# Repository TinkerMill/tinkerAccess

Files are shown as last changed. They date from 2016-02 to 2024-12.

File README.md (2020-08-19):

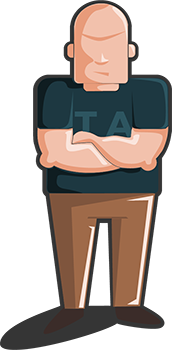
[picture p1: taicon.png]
taicon


# tinkerAccess
The tinkerAccess system is a Raspberry Pi based access control system that can be used to prevent unauthorized users from using devices that require special training. It could also conceivably be used to control electronic lock boxes or doors.

The system was originally designed and created by Matt Stallard, Ron Thomas, and Matt Peopping for TinkerMill a makerspace in Longmont, CO. It is continually being maintained and enhanced by other contributors in the community.

### Install the tinkerAccess system

There are two main components to the system. If you intend to use the client and server software on separate physical devices, then you will want to review the individual documents regarding the installation, configuration, and operation of each respective piece.

- [tinker-access-server](/tinker_access_server/README.md) 
- [tinker-access-client](/tinker_access_client/README.md)

If however, you intend to use both the server and client on the same physical device, then you can follow these simple instructions. You will need to complete these client [prerequisites](/tinker_access_client/docs/prerequisites.md) before running the install script. 

From the Pi terminal:

```
git clone https://github.com/TinkerMill/tinkerAccess.git
cd tinkerAccess
sudo bash install.sh
```

After running the installation script, the configuration files for both the server and client are created, but they need to be modified for a proper setup, before rebooting or restarting the services to take effect.

Edit the server configuration file:

```
sudo nano /opt/tinkeraccess/server.cfg
```

Edit the client configuration file:

```
sudo nano /etc/tinker-access-client.conf
```

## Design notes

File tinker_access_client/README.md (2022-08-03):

# tinker-access-client

The tinker-access-client is the client piece of the tinkerAccess system, a [Raspberry Pi](https://www.raspberrypi.org/products/) based access control system that can be used to prevent unauthorized users from using devices that require special training. It could also conceivably be used to control electronic lock boxes or doors.

The system was originally designed and created by [Matt Stallard](https://github.com/mstallard), [Ron Thomas](https://github.com/RonaldThomas), and [Matt Peopping](https://github.com/analogpixel) for [TinkerMill](http://www.tinkermill.org) a makerspace in [Longmont, CO](https://www.google.com/maps/place/Longmont,+CO/@40.1679379,-105.1678944,12z/data=!3m1!4b1!4m5!3m4!1s0x876bf908d5cc3349:0xc17da1eef3a32735!8m2!3d40.1672068!4d-105.1019275). It is continually being maintained and enhanced by other contributors in the community.

The client software is a [Python 2.7](https://www.python.org/download/releases/2.7/) service designed to run on the [Raspberry Pi OS](https://www.raspberrypi.org/downloads/raspberry-pi-os/). The service is responsible for coordinating activity between the RPi's peripherals (i.e., RFID reader, LCD, etc.) and the GPIO, as well as communicating with the [tinker-access-server](/tinker_access_server/README.md) for activity logging, authentication, and authorization.

Official releases of the client software are packaged and published to [PyPI - the Python Package Index ](https://pypi.python.org/pypi/tinker-access-client/)  

## Prerequisites
You will need to complete these [prerequisites](docs/prerequisites.md) before installing the tinker-access-client.

## Installing the tinker-access-client:

By default, the tinker-access-client is installed as a service that starts immediately, as well as upon reboot of the device.

Use the following command to get the latest version of the client:
```
sudo pip install --upgrade --force-reinstall --ignore-installed --no-cache-dir tinker-access-client --no-binary tinker-access-client
```

Query the client status:
```
sudo tinker-access-client status
```

If the client successfully starts, then the expected status should be *'idle'*. However, the client service will likely not start up at first, and the returned status will be *'terminated'*. The reason for this is that the default client configuration settings will likely not work without some changes. Therefore a client configuration file needs to be added and modified. Get an example client config file directly from the GitHub repo, and then modify it:
```
sudo wget https://raw.githubusercontent.com/TinkerMill/tinkerAccess/master/tinker_access_client/config_file/tinker-access-client.conf -P /etc --backups=1
sudo nano /etc/tinker-access-client.conf
```

The example configuration file has the most commonly used options, many of which are commented out. The *Options* section below lists all of the possible options that can be set in the config file. The command line configuration options all start with --, but the equivalent config file name to be used in the config file is shown in square brackets [ ]. Modify the config file to match your tinker-access-client node wiring and setup, then save the file.

Start the client service again and recheck the status:
```
sudo tinker-access-client start
sudo tinker-access-client status
```

If the client status still does not come back as *'idle'*, then check the log file to get an idea as to why the client service is not starting:
```
less /var/log/tinker-access-client.log
```

See the [development guide](docs/development.md) for special installation instructions, best practices and other helpful information for maintaining and enhancing the code for the future.

## Upgrading the tinker-access-client:

To upgrade to the latest version of the client, here are the commands that have worked for me:
```
sudo tinker-access-client stop
sudo pip install --upgrade --force-reinstall --ignore-installed --no-cache-dir tinker-access-client --no-binary tinker-access-client
sudo tinker-access-client --version
sudo tinker-access-client status
```

## Downgrading the tinker-access-client:

To downgrade to a previous version of the client, here are the commands that have worked for me. Replace the version number in the 'pip install' line with the actual desired version number:
```
sudo tinker-access-client stop
sudo tinker-access-client remove
sudo pip install --upgrade --force-reinstall --ignore-installed --no-cache-dir tinker-access-client==2020.6.28.24 --no-binary tinker-access-client
sudo tinker-access-client --version
sudo tinker-access-client status
```

## Using the tinker-access-client command-line tools:
The remaining information in this guide explains some ways to customize the behavior of the client, control the client, and/or get feedback about the state of the client.

All of the following commands and options are available by using the  --help option on the command line.
```
sudo tinker-access-client --help
```

#### Usage:
```
sudo tinker-access-client <command> [options]
```

#### Commands:
- __start__ : This command will start the tinker-access-client process.

- __stop__ : This command will stop the tinker-access-client process.

- __status__ : This command will return the current state of the tinker-access-client (i.e. initialized, idle, in_use, in_training, terminated).

- __update__ : This command will update the tinker-access-client from the [PyPI - the Python Package Index ](https://pypi.python.org/pypi/tinker-access-client/).  

  By default, the latest published version will be installed. Optionally, a second argument can be provided to specify the specific version desired.
  ```
  sudo tinker-access-client update 2017.2.14.441
  ```

- __remove__ : This command will stop the tinker-access-client process, remove the service and all other artifacts installed via PIP.  

- __restart__ : This command will stop and restart the tinker-access-client process, this can be useful to reload after code changes.

#### Options:

The default value of most of these options can be overridden in a config file. Specifying options via the command line can be useful for debugging purposes.

For example creating this file would enable the auto_update feature, and set the logging level to debug:  

File: `/etc/tinker-access-client.conf`
```
[config]
log_level: 10
auto_update: true
```

- __--version__: Show the current version number and exit

- __-h, --help__: Show the help message and exit

- __--config-file=[config_file]__: The location of the config file to use [default:'/etc/tinker-access-client.conf'] a non-default command-line option value will have precedence over a config-file option value

- __--logging-config-file=[logging_config_file]__: The location of a logging config file to use [default:'/etc/tinker-access-client.logging.conf'] If this file is present, it will override the default logging configuration including the --log-level and --log-file options

- __--debug__: Run in the foreground (a.k.a debug mode) [default:'False']

- __--force-update__: By default, the update command will not do an update if the current version matches the latest version published to [PyPI - the Python Package Index ](https://pypi.python.org/pypi/tinker-access-client/). This option bypasses the version check, and will force a re-install [default:'False']

- __--auto-update=[auto_update]__: If configured, the client will periodically check if a newer version has been published to [PyPI - the Python Package Index ](https://pypi.python.org/pypi/tinker-access-client/). If a new version is found, it will be install it automatically.
[default:'False']

- __--auto-update-interval=[auto_update_interval]__: The period (specified in minutes) that the [PyPI - the Python Package Index ](https://pypi.python.org/pypi/tinker-access-client/) should be checked for a new version of the client. [default:5]

- __--log-file=[log_file]__: The path and name of the log file [default:'/var/log/tinker-access-client.log']

- __--status-file=[status_file]__: The path and name of the status file, the contents of this file will always reflect the current state of the client. (i.e. initialized, idle, in_use, in_training, terminated) A missing file indicates the client is not running [default:'/var/log/tinker-access-client.status']

- __--pid-file=[pid_file]__: The path and name of the client daemon's pid file [default:'/var/run/tinker-access-client.pid']

- __--log-level=[log_level]__: The log level to use [default:40]

- __--server-address=[server_address]__: The [tinker-access-server's](../tinker_access_server/README.md) api address
[default:'http://localhost:5000']

- __--device-id=[device_id]__: The unique identifier for this client, as configured in the [tinker-access-server](../tinker_access_server/README.md) [default:'none']

- __--logout-coast-time=[logout_coast_time]__: A fixed number of seconds to wait for the physical machine to stop before disabling power, after the current sense pin goes low. (i.e., a blade to stop spinning etc...) [default:0]

- __--max-power-down-timeout=[max_power_down_timeout]__: The maximum number of seconds to wait for the current sense pin to go low during logout/shutdown [default:None(infinite)]

- __--reboot-on-error=[reboot_on_error]__: Any unhandled errors will cause the device to reboot after the specified --reboot-delay. [default:'False']

  This behavior is only supported on Raspberry Pi devices.

- __--reboot-delay=[reboot_delay]__: The number of seconds to wait before attempting to reboot the device after an unhandled error. [default:5]

- __--pin-logout=[pin_logout]__: The logout button pin [default:16]

- __--pin-power-relay=[pin_power_relay]__: The power relay pin [default:17]

- __--pin-led-red=[pin_led_red]__: The red led pin [default:21]

- __--pin-led-green=[pin_led_green]__: The green led pin [default:19]

- __--pin-led-blue=[pin_led_blue]__: The blue led pin [default:20]

- __--pin-current-sense=[pin_current_sense]__: The current sense pin [default:12]

- __--pin-current-threshold=[pin_current_threshold]__: The current sense detect threshold PWM pin [default:18]

- __--pin-estop=[pin_estop]__: The E-STOP input pin [default:6]

- __--pin-bypass-detect=[pin_bypass_detect]__: The bypass detect input pin [default:13]

- __--pin-3v3-en=[pin_3v3_en]__: The 3.3V enable pin [default:27]

- __--pin-alarm=[pin_alarm]__: The alarm output pin [default:22]

- __--use-estop=[use_estop]__: The E-STOP input pin will be used to detect E-STOP events and automatically logout the user [default:'False']

- __--estop-active-hi=[estop_active_hi]__: The E-STOP input pin is detected as active high if true, otherwise the input is active low [default:'False']

- __--use-bypass-detect=[use_bypass_detect]__: The bypass detect input pin will be monitored to log a tamper or bypass event [default:'False']

- __--use-3v3-en=[use_3v3_en]__: The PCB has a 3.3V enable output pin and will be cycled during start-up or certain errors. This feature should be set for PCB rev 1.4 or higher [default:'False']

- __--use-alarm=[use_alarm]__: The alarm output pin is enabled and will output high during an alarm condition [default:'False']

- __--use-pgm-current-threshold=[use_pgm_current_threshold]__: The PCB has a programmable current detect threshold PWM output and will be set during init to set the current detect threshold. This feature is available on PCB rev 1.4 or higher. If current detection is desired on rev 1.4 PCBs, this feature must be set True. If it is not desired, it can be left set to False [default:'False']

- __--current-detect-setting=[current_detect_setting]__: The current sense detect threshold setting in RMS milliamps [default:'10000']

- __--ct-burden-resistor=[ct_burden_resistor]__: The current transformer burden resistor value in ohms [default:'1000']

- __--ct-turns-ratio=[ct_turns_ratio]__: The current transformer turns ratio [default:'2000']

- __--is-a-door=[is_a_door]__: The device is a door. If defined, it changes the default behavior of the device and enables the remaining door parameters below [default:'False']

- __--door-unlock-time=[door_unlock_time]__: The amount of time the door unlocks in seconds. Only used if the is-a-door parameter is also enabled [default:'10']

- __--door-continuous-unlock=[door_continuous_unlock]__: The door is defined as being able to be held in a continuously unlocked state. Only used if is-a-door parameter is also enabled. This parameter should only be used on door locks that can be left permanently energized. It should not be enabled on non-continuous duty solenoid style locks. The logout button will be used to toggle between the locked and unlocked state. Therefore, the training mode will be disabled if this parameter is set [default:'False']

- __--door-normal-hr-start=[door_normal_hr_start]__: The start of normal hours, when a door can be held in a continuously unlocked state. Only used if is-a-door and door-continuous-unlock parameters are also enabled. The time is defined in 24hr format. The door cannot be held in an unlocked state before this time [default:'730']

- __--door-normal-hr-end=[door_normal_hr_end]__: The end of normal hours, when a door can be held in a continuously unlocked state. Only used if is-a-door and door-continuous-unlock parameters are also enabled. The time is defined in 24hr format. The door will lock if currently unlocked at this time and cannot be held in an unlocked state after this time [default:'2200']

- __--disable-training-mode=[disable_training_mode]__: Disables entering training mode at the device if the logout button is held down for 3 seconds [default:'False']

- __--serial-port-name=[serial_port_name]__: The serial port attached to the RFID reader [default:'/dev/ttyUSB0']

- __--serial-port-speed=[serial_port_speed]__: The serial port speed to use [default:9600]

- __--display-serlcd=[display_serlcd]__: Send commands for the SparkFun LCD-14072 SerLCD display if true, otherwise send commands for the original backpack style display [default:'False']

- __--allow-user-override=[allow_user_override]__: Allows a new user to login and takeover the current user login session [default:'False']

## Tuning the current detection threshold:

Newer PCBs (rev 1.4) have a programmable current detection threshold. Details on how to tune this can be found [here](tuning/README.md).

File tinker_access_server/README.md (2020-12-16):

# tinker-access-server
All the commands below should be executed from the terminal on the relevant TinkerAccess server.

#### Manage the Services

To start/stop/restart the server:
```
sudo service tinkerserver [start/stop/restart]
```

To stop/start/restart the client:
```
sudo service tinkerclient [start/stop/restart]
```

### Device administration
Incorrectly removing a device can cause big problems and
is rarely needed, so the functionality to modify devices
is located in the cli program devicemanager.py.  This program will allow
you to add, delete, and rename a device.

#### Add a new device 
```
cd /opt/tinkeraccess
sudo ./devicemanager.py -a -n "<new device name>"
```
#### Delete a device
This will delete the device from the database, and it will also delete
all user access records from the database. (not user accounts, but
the fact they have access to the device you just deleted.)
```
cd /opt/tinkeraccess
./devicemanager.py -l
sudo ./devicemanager.py -d -i <device ID to be deleted>
```
#### Rename a device
```
cd /opt/tinkeraccess
sudo ./devicemanager.py -r -i <device ID for name change> -n "<new device name>"
```
#### Grant all users access to a device
This command will grant all users access to the device. Any user in the database will be authenicated to use the device. This command
sets the all users column of the device table
```
cd /opt/tinkeraccess
./devicemanager.py -l
sudo ./devicemanager.py -u -i <device ID to grant all user access>
```
#### Remove all users access to a device
This command sets up the device access level on a per user basis. Users will need to be specifically granted access to be authenicated to use the device. This command
clears the all users column of the device table
```
cd /opt/tinkeraccess
./devicemanager.py -l
sudo ./devicemanager.py -c -i <device ID to remove all user access>
```

### User Administration
#### Adding a new user
To add a new user, scan their badge on the card reader.  Once scanned
if the users badge code is not in the database already, the user
will be added to an Inactive Users table.  On the web gui go to:
http://serverip:5000/admin/interface/newuser  and grant access to
the badge you just swiped.
#### Editing a user
once a user exists in the system, you can use the Users tab to modify
what they have access to.  go to http://serverip:5000/admin/interface/user,
select the pencil next to the user you want to edit, and then from there
you can remove or grant access to all the devices currently registered
in the database

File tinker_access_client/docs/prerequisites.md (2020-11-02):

# Prerequisites:
1. Build the custom tinkerAccess [Raspberry Pi HAT](https://www.raspberrypi.org/blog/introducing-raspberry-pi-hats/) as described [here](/Hardware/PCBs/TinkerAccess/).

2. Create a [Raspberry Pi OS](https://www.raspberrypi.org/downloads/raspberry-pi-os/) boot image as described in detail [here](bootimage.md).

3. Modify the Raspberry Pi Configuration.

   Launch the 'Raspberry Pi Configuration' as shown below:

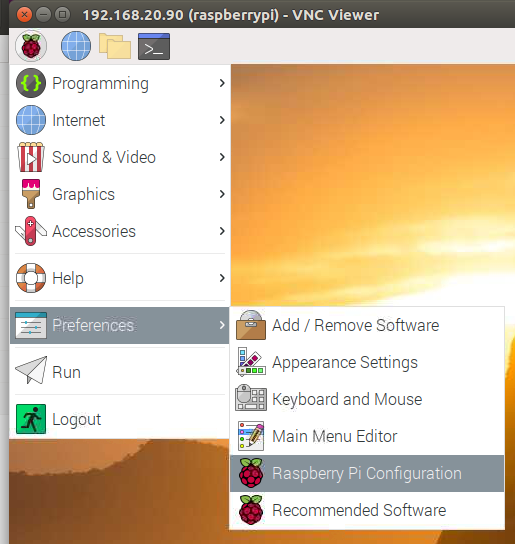
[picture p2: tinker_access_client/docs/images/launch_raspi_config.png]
Raspberry Pi Configuration
   

   Change the Hostname of the client, and change the default password if not completed in an earlier step:

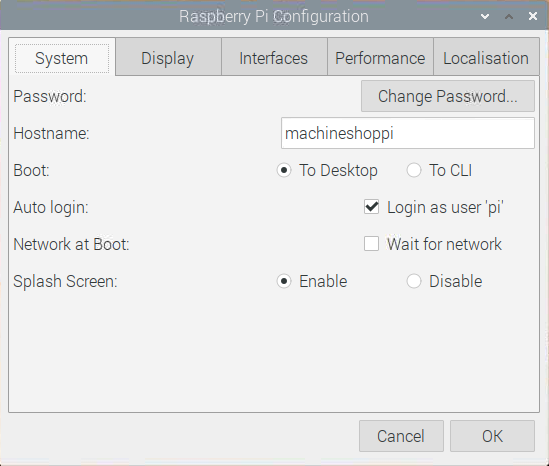
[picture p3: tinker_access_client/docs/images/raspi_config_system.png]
Pi Config System
   

   Setup the Interfaces as shown below:

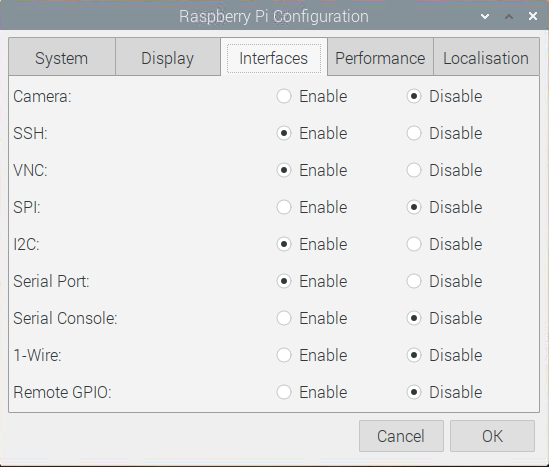
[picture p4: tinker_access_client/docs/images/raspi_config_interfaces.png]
Pi Config Interfaces
   

   SSH and VNC should be enabled for headless remote access to the client. 'I2C' needs to be enabled for the client to communicate to the LCD display. The 'Serial Port' needs to be enabled for the client to communicate to the RFID, but the 'Serial Console' needs to be disabled so that it does not interfere with the RFID communication.

   Reboot the Pi after making changes to the Raspberry Pi Configuration.

4. Reconnect to your Pi via [SSH](https://www.raspberrypi.org/documentation/remote-access/ssh/README.md) or [VNC](https://www.raspberrypi.org/documentation/remote-access/vnc/README.md).

5. Install the python package manager (a.k.a 'pip').

   **IMPORTANT**: If you have just created a new image using the previous mentioned guide, or you are using an existing image...

   Ensure you have the latest version of [pip](https://pip.pypa.io/en/stable) and its related setuptools installed. If you do not complete this step, you will almost certainly __not__ have a good time. Version issues with PIP and its related setuptools can be inconsistent, confusing, and difficult to resolve. It is better to just avoid it now and ensure that they are updated. 

   Many references that you can find, say to upgrade pip with the command 'pip install --upgrade pip setuptools'. However, it is not advisable to upgrade the system version of pip with this method. It can create all sorts of issues if the system maintainer version is upgraded via this method. References to many of these issues are described [here](https://github.com/pypa/pip/issues/5599).

   The recommended upgrade process is shown below:
   ```
   sudo apt update
   sudo apt install python-pip python-setuptools
   ```

6. Install pigpio

   For the PWM current sense level detect output, the Python code uses the PWM features of the pigpio library. Therefore, the pigpio library needs to be installed and the daemon needs to be started at bootup. The following command will ensure the pigpio library is installed and the daemon running at bootup:
   ```
   sudo apt install pigpio
   sudo systemctl enable pigpiod
   sudo reboot
   ```

   After reboot check the status of the pigpiod daemon with the following command:
   ```
   sudo systemctl status pigpiod
   ```
   
7. Continue with [client only install](/tinker_access_client/README.md) or [combined client/server install](/README.md).

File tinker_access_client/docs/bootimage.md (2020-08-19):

## Creating a tinker-access-client boot image:

This document details the steps required to create a [Raspberry Pi OS](https://www.raspberrypi.org/downloads/raspberry-pi-os/) boot image and prepare it for the tinker-access-client.

There are many such guides that you can find, some with much more info, some with much less. I will let you pick your own poison, but it is hard to beat [this guide](https://www.raspberrypi.org/documentation/installation/installing-images/README.md).

The intent of this guide is to document a few additional steps that will facilitate the install in a completely headless mode (i.e., not requiring a monitor and keyboard). In order to do a completely headless setup, there needs to be a method to determine the IP address assigned to the Pi, external to the Pi. Access to the network router/DHCP server would typically be the desired method. If such a method is not available, then the initial stages of setup will need to use a monitor and keyboard, until the IP address can be determined and the SSH and/or VNC services enabled. After that, the setup can continue in a headless mode.

1. Download the [Raspberry Pi OS image](https://www.raspberrypi.org/downloads/raspberry-pi-os/).

   The "Raspberry Pi OS (32-bit) with desktop" is the typical desired image. It is a somewhat light-weight image, in that it does not include all of the recommended software of a full install, but it still includes the desktop.

2. Write the image to an SD card.

   Using your preferred method, write the downloaded image to an SD card. The standard method is the [Raspberry Pi Imager](https://www.raspberrypi.org/documentation/installation/installing-images/README.md). Other methods are described in the link for various OSes.

#### Steps 3-8 are optional. If you do not want to begin the install in a completely headless mode, and are starting with a keyboard and monitor, you can install the imaged SD card in the Pi, power it up, and continue the setup starting at step 9.

3. Mount the *boot* partition of the SD card locally, so that you can add a couple of files to the root directory of the *boot* partition.

4. [Enable SSH for a headless Pi](https://www.raspberrypi.org/documentation/remote-access/ssh/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).

   Create an empty file named *ssh* at the root of the *boot* partition. This will automatically enable the SSH service when the Raspberry Pi boots up, which is normally disabled by default.

   From the root directory of the locally mounted *boot* partition, run the following command:
   ```
   sudo touch ssh
   ```

5. [Setup WiFi for a headless Pi](https://www.raspberrypi.org/documentation/configuration/wireless/headless.md).

   Create a file named *wpa_supplicant.conf* in the root directory of the *boot* partition that contains your WiFi credentials. On the initial boot, the Raspberry Pi will copy this file to the appropriate location and use it to connect to your WiFi network so that you can continue to configure it via SSH.

   From the root directory of the locally mounted *boot* partition, run the following command:
   ```
   sudo nano wpa_supplicant.conf
   ```

   Paste the following contents into the file and save. Modify the SSID and password to match your actual WiFi access point credentials.
   ```
   ctrl_interface=DIR=/var/run/wpa_supplicant GROUP=netdev
   update_config=1
   country=US
   
   network={
    ssid="<Name of your wireless LAN>"
    psk="<Password for your wireless LAN>"
   }
   ```

6. Unmount the *boot* partition, remove the SD card, install it in the Raspberry Pi, and power it up.

7. Enable the VNC server to facilitate completion of the install via the desktop on a VNC client running locally.

   From your local machine, ssh into the Raspberry Pi. Use the actual IP address assigned to the Pi. For the default *pi* username, the default password is *raspberry*:
   ```
   ssh pi@192.168.20.90
   ```

   Enable the VNC server via *raspi-config*:
   ```
   sudo raspi-config
   ```

   Select *Interfacing Options* from the raspi-config menu:

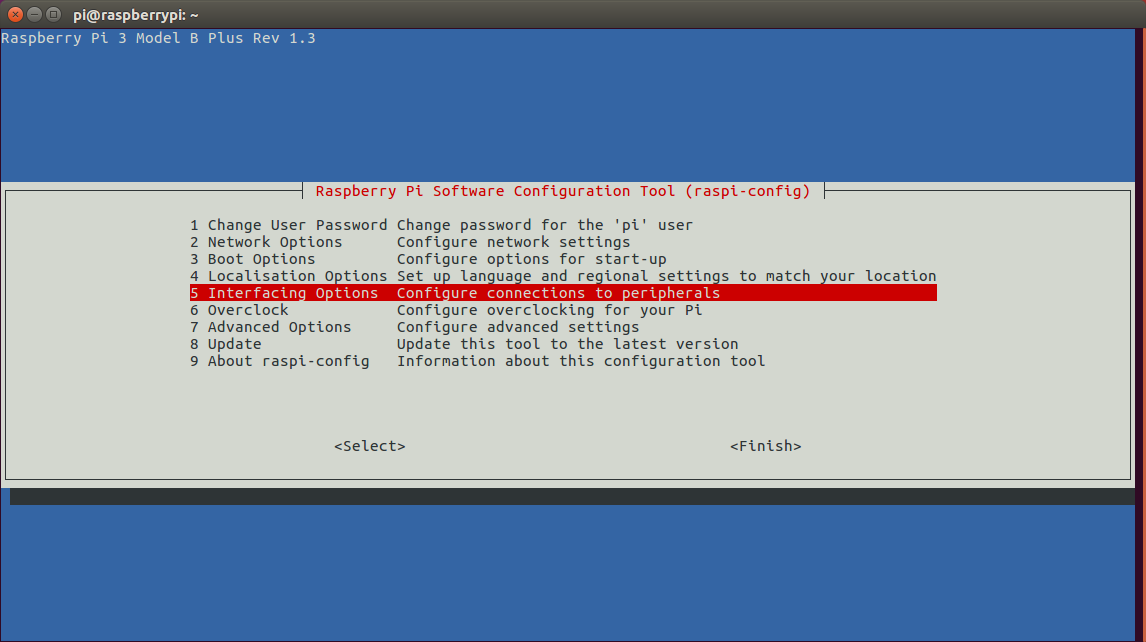
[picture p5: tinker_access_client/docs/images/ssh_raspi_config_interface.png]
raspi-config Interfacing Options
   

   Next, select *VNC* from the raspi-config menu, and then enable the VNC server.

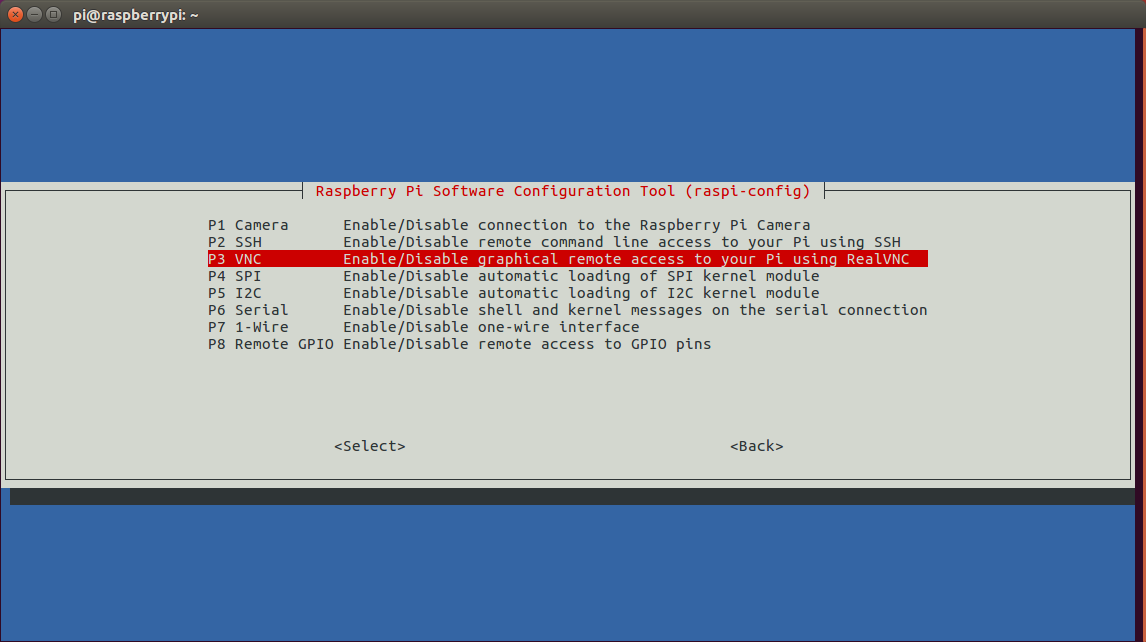
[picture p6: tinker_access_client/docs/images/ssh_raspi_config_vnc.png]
raspi-config VNC
   

   After enabling the VNC server, exit the raspi-config, and exit the SSH session. The VNC server should be started and does not require a reboot of the Pi.

8. Connect to the Raspberry Pi via a RealVNC Viewer client running on your local machine.

   Use the assigned IP address to connect and use the default username *pi* and password *raspberry*. The default password can be changed in the next step.

9. Complete the Raspberry Pi OS installation and update.

   After the initial boot, the following dialog box should be displayed to continue the installation process. Click 'Next' to continue the setup:

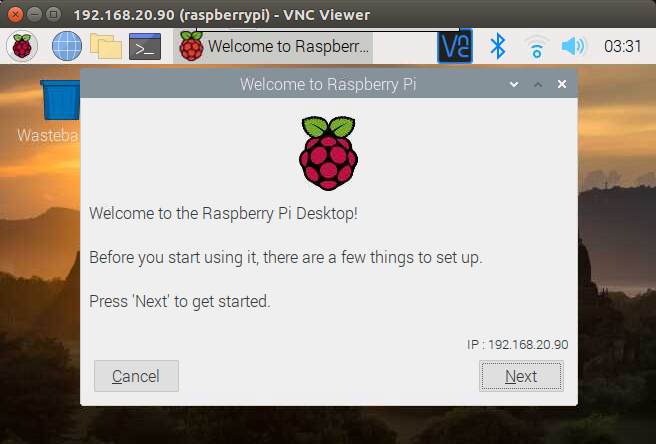
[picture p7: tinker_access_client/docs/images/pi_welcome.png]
Installation Welcome
   

   Set the Country and Timezone:

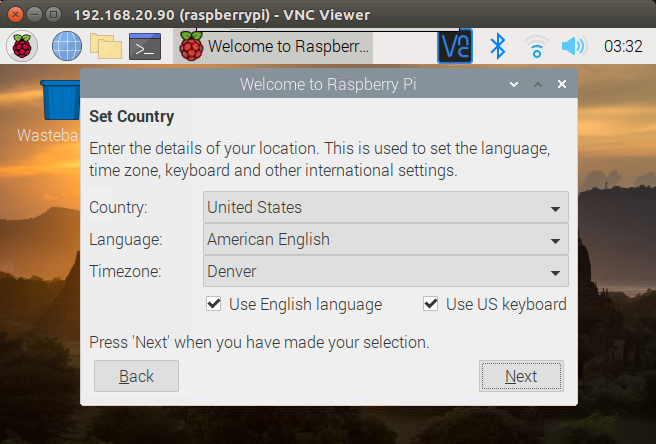
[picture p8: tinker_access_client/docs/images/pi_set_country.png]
Installation Set Country
   

   Change the default *pi* username password in this step:

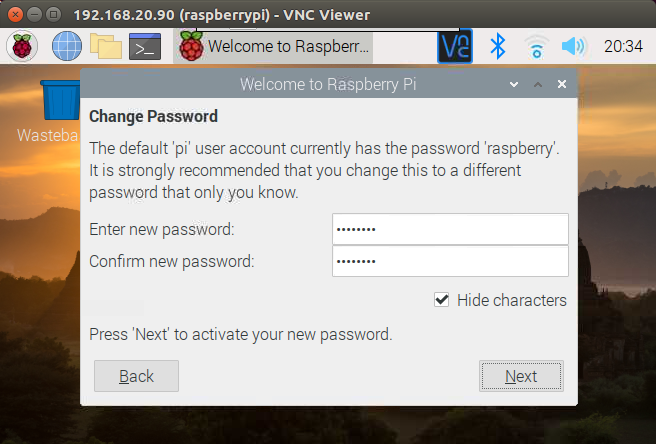
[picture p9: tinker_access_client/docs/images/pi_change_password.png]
Installation Change Password
   

   Leave the 'fill entire screen' checkbox unchecked:

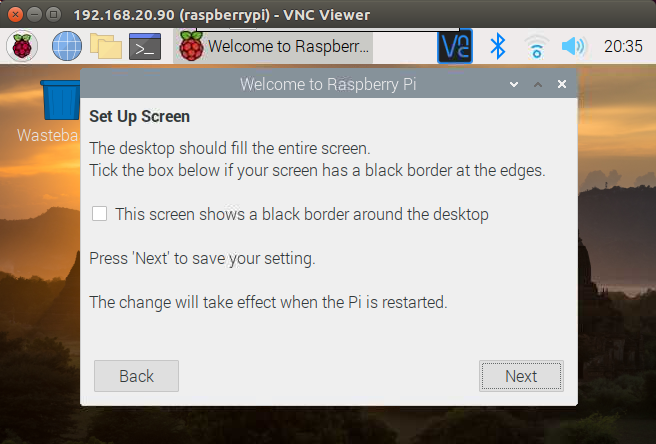
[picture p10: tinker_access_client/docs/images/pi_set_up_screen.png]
Installation Set Up Screen
   

   Click 'Next' to download and install updates to the OS. This will take a while to complete:

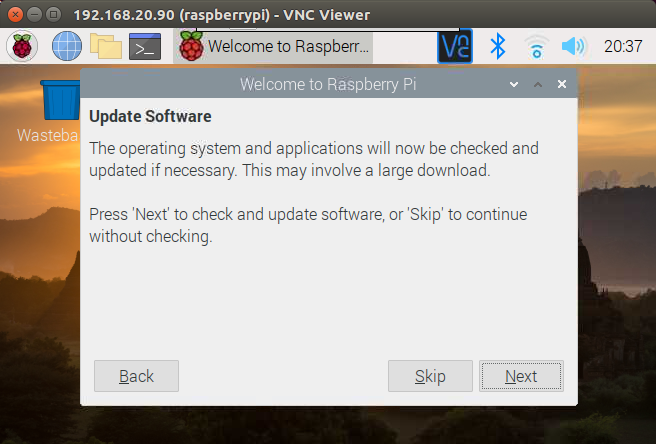
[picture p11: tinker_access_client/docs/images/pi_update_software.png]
Installation Update Software
   

   If the download and update fails for any reason, the update can be completed at the command line with the following commands:
   ```
   sudo apt update
   sudo apt upgrade
   ```

   After the update completes, the following dialog will be displayed. If you want to change the default screen resolution when connected to the Pi via VNC, without a monitor, do not reboot just yet, and click 'Later'. Complete step 10 before rebooting. Otherwise, if you do not want to change the default screen resolution, go ahead and reboot the Pi by clicking 'Restart':

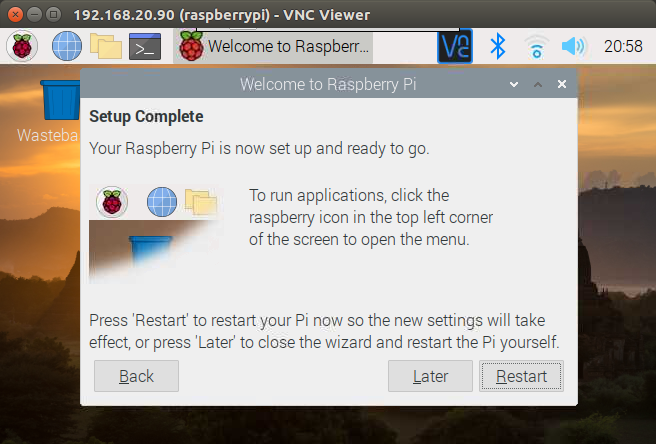
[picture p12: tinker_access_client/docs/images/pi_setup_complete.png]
Installation Setup Complete
   

10. Change the default screen resolution.

    This step is optional, but should be completed if you want the default VNC screen resolution to be something larger, when no monitor is connected. Edit the */boot/config.txt* file to change the default screen resolution. From a terminal window on the Pi, run the following command:
    ```
    sudo nano /boot/config.txt
    ```

    Uncomment and modify the contents of the following lines to look like the following. This will change the screen resolution to CEA mode, 1920x1080, 60Hz, 16:9 aspect ratio:
    ```
    # uncomment if hdmi display is not detected and composite is being output
    hdmi_force_hotplug=1
    
    # uncomment to force a specific HDMI mode (this will force VGA)
    hdmi_group=1
    hdmi_mode=16
    ```

    Reboot the Pi:
    ```
    sudo reboot
    ```
    
#### The setup of the Raspberry Pi OS boot image for the tinker-access-client is complete. You can continue with the rest of the client [prerequisites](prerequisites.md)

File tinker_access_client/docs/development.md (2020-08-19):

### Development:

For development purposes, the client code can be installed from many different types of locations (i.e., the local file system and other [GitHub](https://github.com) branches). You can find additional examples [here](http://www.developerfiles.com/pip-install-from-local-git-repository/).

You can use the [-e, --editable](https://pip.pypa.io/en/latest/reference/pip_install/#cmdoption-e) flag to install the package in editable mode. This will create a symlink from dist-packages to your local development directory so you do not need to re-install each time you change a file.
```
sudo pip install -e <path to your local development directory where setup.py resides>
```

I generally do not do development on the Raspberry Pi. I setup a task to synchronize my files from my development machine and the Pi. PyCharm makes this easy with [deployment configuration](https://www.jetbrains.com/help/phpstorm/2016.3/deployment.html), but there are many other options to synchronize a directory with a remote directory.

Here are examples of my [connection](images/deployment_configuration_connection.png) & [mappings](images/deployment_configuration_mappings.png) configuration.

After changing a local file, ssh into the Raspberry Pi and restart the client software to see your changes take affect.
```
sudo tinker-access-client restart
```

##### Run in stand-alone mode:

When you install the client using [-e, --editable ](https://pip.pypa.io/en/latest/reference/pip_install/#cmdoption-e) option flag, the client will NOT install the service piece. You will get the command line support tools, but you will not automatically get the service piece. This means that any service related commands will not work (i.e., *sudo service tinker-access-client start*) and the client will not automatically start upon boot of the device.

If you really do want the service piece, you can create it with these commands, pointing the symlink to the same location that you installed your package from using the -e flag. Normally this is not required.
```
# create the startup service symlink manually
sudo ln -sf ~/projects/tinkerAccess/tinker_access_client/tinker_access_client/Service.py /etc/init.d/tinker-access-client

# grant execute permission on the Service.py file
sudo chmod 0755 ~/projects/tinkerAccess/tinker_access_client/tinker_access_client/Service.py

#configure the service to start on boot
sudo update-rc.d -f tinker-access-client defaults 91

#start the service
sudo service tinker-access-client start
```

You can run the client as a stand alone script in the foreground if you do not want to install a full blown service. This is helpful for testing and development purposes. You can also control the configuration in debug mode with additional command line switches. However, if you want complete control via the command line, and do not want the config file overriding your command line switches, be sure to rename or delete the */etc/tinker-access-client.conf* file.
```
sudo tinker-access-client start --debug
```

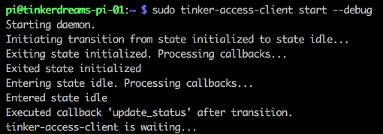
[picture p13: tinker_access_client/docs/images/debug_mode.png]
debug


### Testing/Emulation:

See the [testing](/tinker_access_client/tests/README.md) documentation for more info.

### Logging:

If you are not using debug mode, but want to watch the log messages you can use the following command:
```
sudo tail -f /var/log/tinker-access-client.log
```

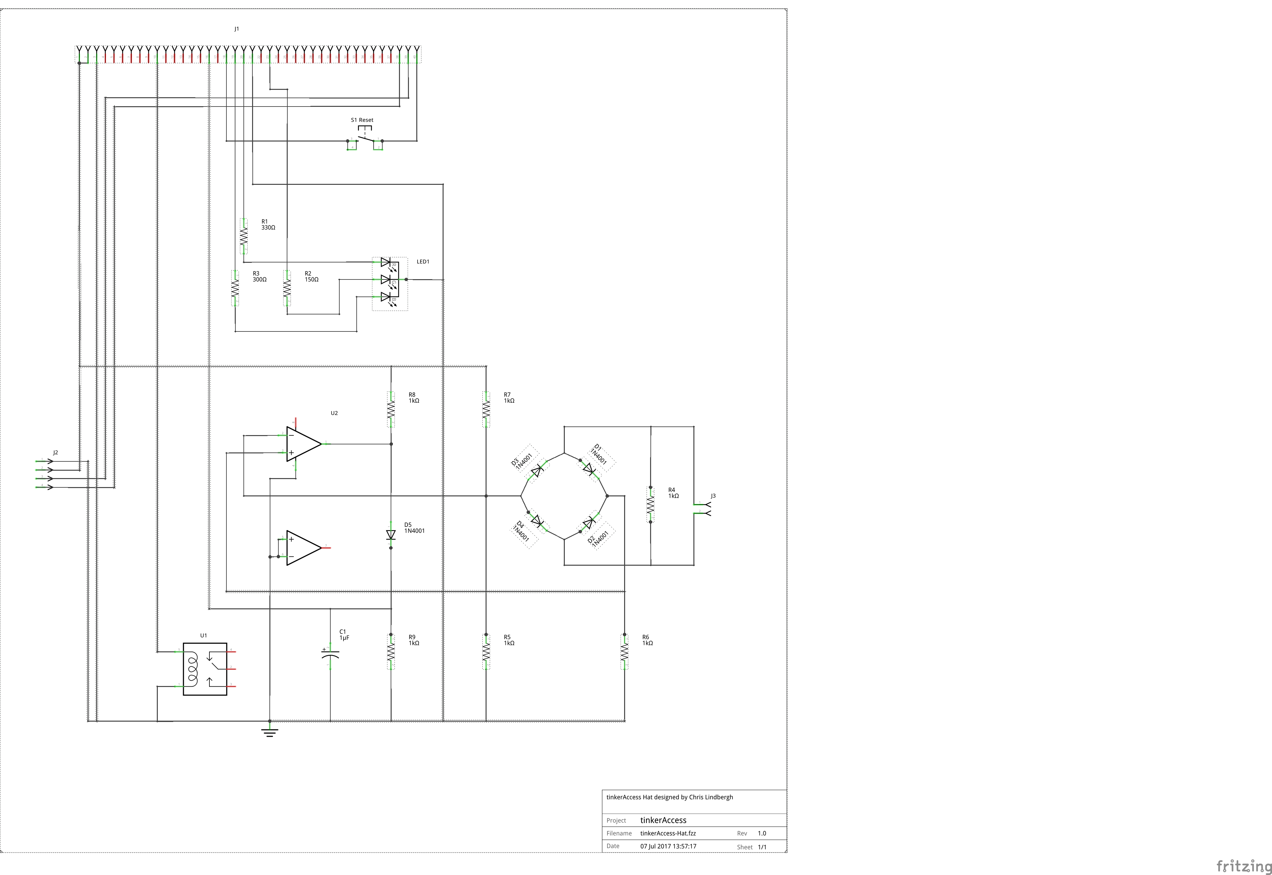
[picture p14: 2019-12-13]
docs/PCBFiles/tinkerAccess-Hat_schem.png

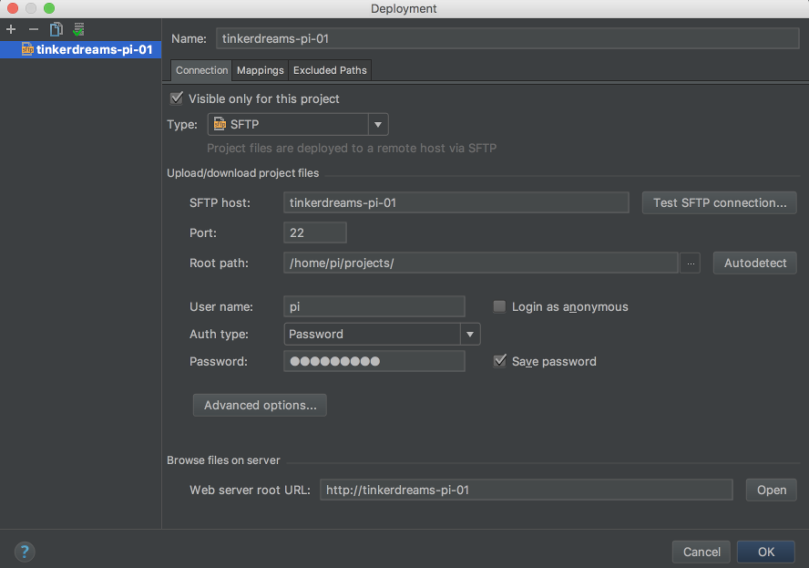
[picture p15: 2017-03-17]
tinker_access_client/docs/images/deployment_configuration_connection.png

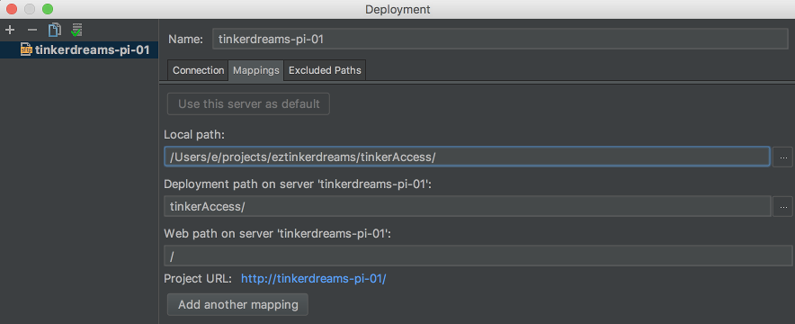
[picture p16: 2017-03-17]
tinker_access_client/docs/images/deployment_configuration_mappings.png

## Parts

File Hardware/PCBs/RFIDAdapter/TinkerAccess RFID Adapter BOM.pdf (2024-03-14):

# TinkerAccess RFID Adapter v1.0 BOM

RefDes | Qty | Description | Package / Footprint | Manufacturer | Manufacturer Part # | Vendor | Vendor Part # | JLCPCB Part #
C1 | 1 | Capacitor, MLCC, 1uF, 10V, 10%, X7R, 0603 | 0603 | Samsung Electro-Mechanics | CL10B105KP8NNNC | DigiKey | 1276-1946-2-ND (https://www.digikey.com/products/en?keywords=1276-1946-2-ND) | C15849
C2 | 1 | Capacitor, MLCC, 0.1uF, 50V, 5%, X7R, 0603 | 0603 | Yageo | CC0603JRX7R9BB104 | DigiKey | 311-1779-2-ND (https://www.digikey.com/products/en?keywords=311-1779-2-ND) | C14663
J1 | 1 | Connector, Terminal Block, 2 Pos, 5mm | Through Hole | Wurth | 691137710002 | DigiKey | 732-10955-ND (https://www.digikey.com/products/en?keywords=732-10955-ND)
U1 | 1 | Connector, Male Header, 5 Pos, Single Row, Gold, 2mm Spacing, 0.142” Head, 0.110” Tail | Through Hole | Sullins Connector | NRPN051PAEN-RC | DigiKey | S5800-05-ND (https://www.digikey.com/products/en?keywords=S5800-05-ND)
U1 | 1 | Connector, Male Header, 7 Pos, Single Row, Gold, 2mm Spacing, 0.142” Head, 0.110” Tail | Through Hole | Sullins Connector | NRPN071PAEN-RC | DigiKey | S5800-07-ND (https://www.digikey.com/products/en?keywords=S5800-07-ND)
U2 | 1 | IC, Single RS-232 Receiver, SOT23-5 | SOT23-5 | Maxim | MAX3181EUK+T | DigiKey | MAX3181EUK+CT-ND (https://www.digikey.com/products/en?keywords=MAX3181EUK+CT-ND) | C2671244

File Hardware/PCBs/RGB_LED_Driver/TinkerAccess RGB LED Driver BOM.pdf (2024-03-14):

# TinkerAccess RGB LED Driver v1.0 BOM

RefDes | Qty | Description | Package / Footprint | Manufacturer | Manufacturer Part # | Vendor | Vendor Part # | JLCPCB Part #
J1 | 1 | Connector, Terminal Block, 5 Pos, 2.54mm | Through Hole | On Shore Technology | OSTVN05A150 | DigiKey | ED10564-ND (https://www.digikey.com/products/en?keywords=ED10564-ND)
J2 | 1 | Connector, Terminal Block, 4 Pos, 2.54mm | Through Hole | On Shore Technology | OSTVN04A150 | DigiKey | ED10563-ND (https://www.digikey.com/products/en?keywords=ED10563-ND)
Q1, Q2, Q3 | 3 | Transistor, N-Channel MOSFET, 50V, 210 mA, 3.5 Ohm RDSon, SOT323 | SOT323 | On Semi | BSS138W | DigiKey | BSS138WCT-ND (https://www.digikey.com/products/en?keywords=BSS138WCT-ND) | C24553
R1, R2, R3 | 3 | Resistor, Thick Film, 10K, 1%, 1/10W, 0603 | 0603 | Yageo | RT0603FRE0710KL | DigiKey | YAG2321TR-ND (https://www.digikey.com/products/en?keywords=YAG2321TR-ND) | C216802

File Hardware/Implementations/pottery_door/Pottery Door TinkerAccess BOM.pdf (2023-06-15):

# TinkerAccess Enclosure

Qty | Description | Manufacturer | Manufacturer PN | Vendor | Vendor PN | Cost | Notes
1 | Enclosure, Metal | Enclosure that came with magnetic door lock kit
1 | Backpanel, Custom | TinkerMill | Backplate to mount all component in enclosure
1 | Wall Transformer, 120VAC Plugin, 16.5VAC 40VA Output | MG Electronics | MGT1640P | | | | Came with magnetic door lock kit
1 | Motion Detector | Bosch | DS161 | Came with magnetic door lock kit
1 | Magnetic Door Lock | Rosslare Security | LK-M06L | Came with magnetic door lock kit
1 | Push to Exit Button | Alarm Controls | TS-2 | Came with magnetic door lock kit
1 | Power Supply / Charger | Altronix | AL624 | Came with magnetic door lock kit
1 | Raspberry Pi Zero W with Headers | Raspberry Pi Foundation | Pi Zero WH | SparkFun | DEV-15470 (https://www.sparkfun.com/products/15470) | $14.00
1 | Memory Card, microSD, 16GB, Class 10 | SanDisk | SDSQUAR-016G-GN6MA | Amazon | SDSQUAR-016G-GN6MA (https://www.amazon.com/dp/B073K14CVB/ref=twister_B08CLNX58K?_encoding=UTF8&th=1) | $6.19
1 | Connector, U.FL, SMD | Hirose Electric | U.FL-R-SMT-1(10) | DigiKey | H11891CT-ND (https://www.digikey.com/products/en?keywords=H11891CT-ND) | $1.22 Solder to Pi Zero W for external antenna
1 | Raspberry Pi Compute Module 4 Antenna Kit | Raspberry Pi Foundation | YH2400-5800-SMA-108 | Adafruit | 4793 (https://www.adafruit.com/product/4793) | $5.00
1 | TinkerAccess Hat, v1.4 | TinkerMill
1 | TinkerAccess RFID Adapter, v1.0 | TinkerMill
1 | TinkerAccess RGB LED Driver, v1.0 | TinkerMill
1 | LCD, 16x2 Basic, Black on Green, 3.3V | SparkFun | LCD-09053 | SparkFun | LCD-09053 (https://www.sparkfun.com/products/9053) | $16.95
1 | LCD I2C Backpack | HiLetgo | 03-01-1980 | Amazon | 03-01-1980 (https://www.amazon.com/HiLetgo-Interface-LCD1602-Address-Changeable/dp/B00VC2NEU8?hvadid=385286500280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) | $5.95
1 | Adapter, Qwiic | SparkFun | DEV-14495 | SparkFun | DEV-14495 (https://www.sparkfun.com/products/14495) | $1.50 Needs to be soldered to LCD I2C and power pins
1 | Cable, Qwiic, 200mm | SparkFun | PRT-14428 | SparkFun | PRT-14428 (https://www.sparkfun.com/products/14428) | $1.50
1 | Latching Push Button, 19mm, 1-NO/NC, 12VDC Blue LED | Mxuteuk | L-19-POWER-T-BU | Amazon | L-19-POWER-T-BU (https://www.amazon.com/gp/product/B083SDTZVV/ref=ppx_yo_dt_b_asin_title_o07_s00?ie=UTF8&psc=1) | $5.89
1 | DC/DC Converter, 12/24VDC Input, 5V / 3A Output, 15W | Tobsun | EA15-5V | Amazon | EA15-5V (https://www.amazon.com/BINZET-Converter-Regulator-Regulated-Transformer/dp/B00J3MHRNO) | $8.59
1 | DIN Rail, Slotted, 15mm, 5.5mm height, 1m length, Plated Steel. Pkg of 2 | Konnect-It | DN-R15S1-2 | Automation Direct DN-R15S1-2 (https://www.automationdirect.com/adc/shopping/catalog/enclosures_-z-_subpanels_-z-_thermal_management_-z-_lighting/enclosure_parts_-a-_accessories/din_rails/d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) | $9.50
1 | Terminal Block, Single-Level, Mini, Size 26 - 12 AWG, Gray, 20A, 300V Rated, 15mm DIN Rail Mount, Pkg of 25 | Konnect-It | KN-M12GRY-25 | Automation Direct KN-M12GRY-25 (https://www.automationdirect.com/adc/shopping/catalog/terminal_blocks/konnect-it_din-rail_terminal_blocks/mini_terminal_blocks/kn-m12gry-25) | $9.75
1 | Terminal Block End Cover, Gray, For use with KN-M12 or KN-M10 Series Terminal Blocks, Pkg of 10 | Konnect-It | KN-ECMGRY-10 | Automation Direct KN-ECMGRY-10 (https://www.automationdirect.com/adc/shopping/catalog/terminal_blocks/konnect-it_din-rail_terminal_blocks/end_covers/kn-ecmgry-10) | $4.00
1 | Terminal Block, Single-Level, Mini, Size 26 - 12 AWG, Blue, 20A, 300V Rated, 15mm DIN Rail Mount, Pkg of 25 | Konnect-It | KN-M12BLU-25 | Automation Direct KN-M12BLU-25 (https://www.automationdirect.com/adc/shopping/catalog/terminal_blocks/konnect-it_din-rail_terminal_blocks/mini_terminal_blocks/kn-m12blu-25) | $9.75
1 | Terminal Block End Cover, Blue, For use with KN-M12 or KN-M10 Series Terminal Blocks, Pkg of 10 | Konnect-It | KN-ECMBLU | Automation Direct KN-ECMBLU (https://www.automationdirect.com/adc/shopping/catalog/terminal_blocks/konnect-it_din-rail_terminal_blocks/end_covers/kn-ecmblu) | $4.00
1 | Terminal Block End Bracket, Sanp-On Type, 8mm Wide, For use with 15mm DIN Rail, Pkg of 10 | Konnect-It | KN-EB5-10 | Automation Direct KN-EB5-10 (https://www.automationdirect.com/adc/shopping/catalog/terminal_blocks/konnect-it_din-rail_terminal_blocks/end_brackets/kn-eb5-10) | $5.50
4 | Machine Screw, Nylon, Pan Head, Phillips, #2-56 x 1/4” | B&F Fastener Supply | NY PMS 256 0025 PH | DigiKey | H530-ND (https://www.digikey.com/products/en?keywords=H530-ND) | $0.19 Mounting RGB LED Driver to PCB Standoff
4 | Hex Standoff, Aluminum, 3/16” Hex, Male-Female #2-56, 1/4” Length | RAF Electronic Hardware | 4501-256-AL | DigiKey | 1772-1104-ND (https://www.digikey.com/products/en?keywords=1772-1104-ND) | $0.98 Between RGB LED Driver to Backplate
6 | Machine Screw, Nylon, Pan Head, Phillips, #4-40 x 1/4” | B&F Fastener Supply | NY PMS 440 0025 PH | DigiKey | H542-ND (https://www.digikey.com/products/en?keywords=H542-ND) | $0.09 Mounting TinkerAccess Hat and Raspberry Pi to PCB Standoff
2 | Hex Standoff, Aluminum, 3/16” Hex, Male-Female #4-40, 1” Length | RAF Electronic Hardware | 4513-440-AL | DigiKey | 1772-1054-ND (https://www.digikey.com/products/en?keywords=1772-1054-ND) | $0.60 Between TinkerAccess Hat and Backpanel
2 | Hex Standoff, Aluminum, 3/16” Hex, Male-Female #4-40, 5/8” Length | RAF Electronic Hardware | 4507-440-AL | DigiKey | 1772-1206-ND (https://www.digikey.com/products/en?keywords=1772-1206-ND) | $0.56 Between TinkerAccess Hat and Raspberry Pi
4 | Hex Standoff, Aluminum, 3/16” Hex, Male-Female #4-40, 5/16” Length | RAF Electronic Hardware | 4502-440-AL | DigiKey | 1772-1253-ND (https://www.digikey.com/products/en?keywords=1772-1253-ND) | $0.46 Between Raspberry Pi and Backpanel
4 | Machine Screw, Nylon, Pan Head, Phillips, #2-56 x 3/4” | B&F Fastener Supply | NY PMS 256 0075 PH | DigiKey | H538-ND | $0.09 Mounting LCD to Enclosure Cover
4 | Round Spacer, Nylon, 3/16” Dia, #2, 1/4” | Bivar Inc | 9913-250 | DigiKey | 492-1044-ND (https://www.digikey.com/products/en?keywords=492-1044-ND) | $0.10 Between LCD and Enclosure Cover
8 | Hex Nut, Nylon, #2-56 | Essentra Components | 0400256HN | DigiKey | RPC7088-ND (https://www.digikey.com/products/en?keywords=RPC7088-ND) | $1.00 Mounting LCD to Enclosure Cover
4 | Machine Screw, Nylon, Pan Head, Phillips, #6-32 x 1/4” | B&F Fastener Supply | NY PMS 632 0025 PH | DigiKey | H554-ND (https://www.digikey.com/products/en?keywords=H554-ND) | $0.13 Mounting Charger to PCB Standoff
4 | Hex Standoff, Nylon, 1/4” Hex, Male-Female #6-32, 3/8” Length | Keystone Electronics | 4815 | DigiKey | 36-4815-ND (https://www.digikey.com/products/en?keywords=36-4815-ND) | $0.54 Between Charger and Backpanel

$130.08

# Outdoor Remote RFID Enclosure

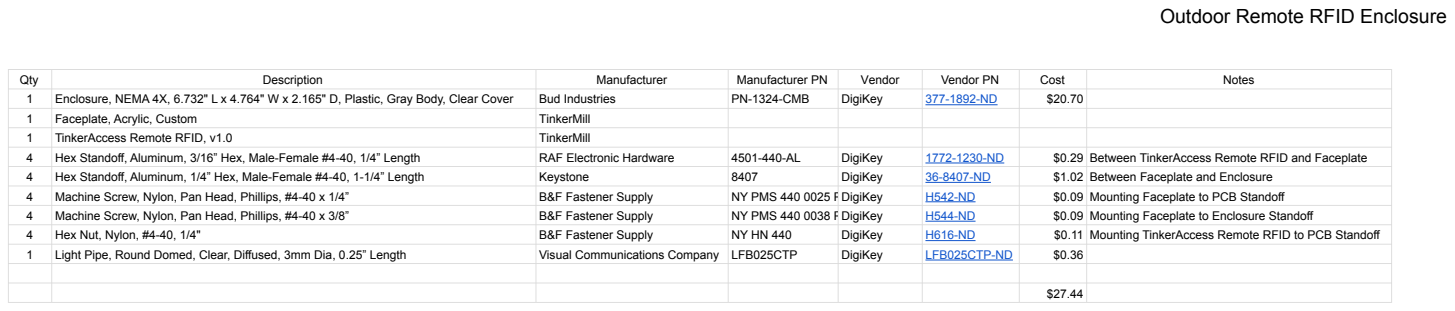
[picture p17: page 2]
Qty; Description; Manufacturer; Manufacturer PN; Vendor; Vendor PN; Cost; Notes; Enclosure, NEMA 4X, 6.732" L x 4.764" W x 2.165" D, Plastic, Gray Body, Clear Cover; Bud Industries; PN-1324-CMB; DigiKey; Faceplate, Acrylic, Custom; TinkerMill; TinkerAccess Remote RFID, v1.0; Hex Standoff, Aluminum, 3/16” Hex, Male-Female #4-40, 1/4” Length; RAF Electronic Hardware; $0.29 Between TinkerAccess Remote RFID and Faceplate; Hex Standoff, Aluminum, 1/4” Hex, Male-Female #4-40, 1-1/4” Length; Keystone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

# Lock Button Enclosure

Qty | Description | Manufacturer | Manufacturer PN | Vendor | Vendor PN | Cost | Notes
1 | Enclosure, Pushbutton, 1 hole, 22mm, 70 x 70 x 74mm (HxWxD), Wall Mount, Thermoplastic ABS, Gray, Screw cover | Pilot Devices | SA103SL | Automation Direct | SA103SL (https://www.automationdirect.com/adc/shopping/catalog/enclosures_-z-_subpanels_-z-_thermal_management_-z-_lighting/enclosures/pushbutton_enclosures/22mm/sa103sl) | $8.25
1 | Pushbutton, 22mm, 6V RGB, Momentary | Elewind | PM221-11E/42RGB/12V/S | Adafruit | 3423 (https://www.adafruit.com/product/3423) | $16.50
2 | Quick Connect Female Terminals, 18-22 AWG Crimp Connector Fully Insulated | Panduit | DNF18-111FIB-M | DigiKey | 298-10548-ND (https://www.digikey.com/products/en?keywords=298-10548-ND) | $0.47
2 | Crimp Housing, 0.100" Spacing, 2-position | Molex | 0050579002 | DigiKey | WM2800-ND (https://www.digikey.com/products/en?keywords=WM2800-ND) | $0.33
4 | Crimp Terminals, 22-24AWG | Molex | 0016020103 | DigiKey | WM2512-ND (https://www.digikey.com/products/en?keywords=WM2512-ND) | $0.20

$27.15

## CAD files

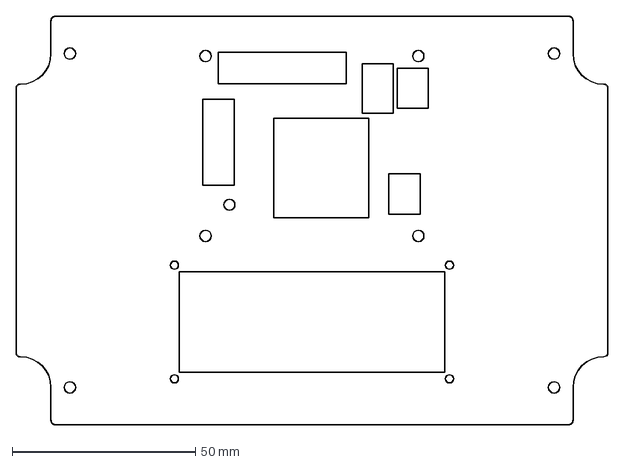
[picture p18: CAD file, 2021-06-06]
Hardware/Enclosures/TinkerAccess_Faceplate_Horizontal.dxf
161.4 x 111.4 mm

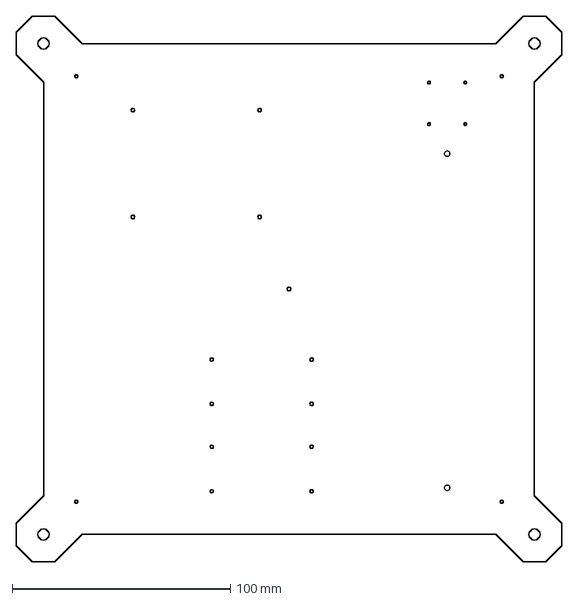
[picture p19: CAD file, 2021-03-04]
Hardware/Implementations/front_door/Front_Door_TinkerAccess_Backplate.dxf
250.0 x 250.0 mm

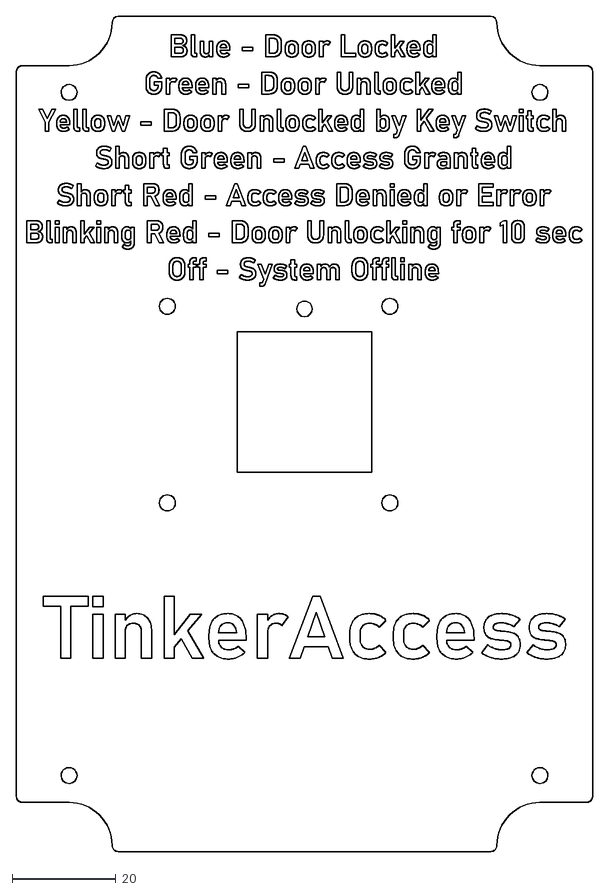
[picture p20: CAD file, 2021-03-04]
Hardware/Enclosures/Remote_RFID_TinkerAccess_Faceplate.dxf
111.4 x 161.4

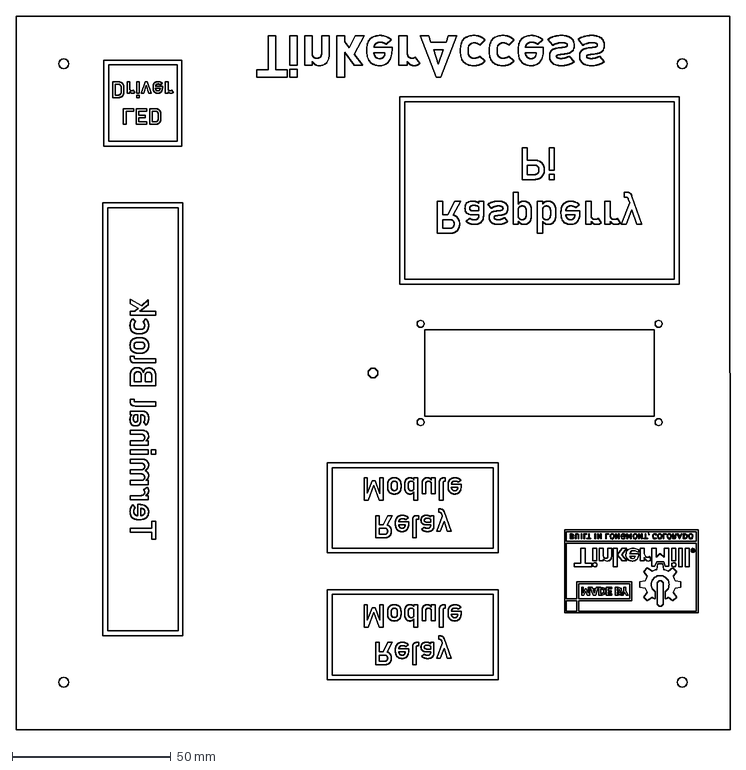
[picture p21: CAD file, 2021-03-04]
Hardware/Implementations/front_door/Front_Door_TinkerAccess_Faceplate.dxf
225.0 x 225.0 mm

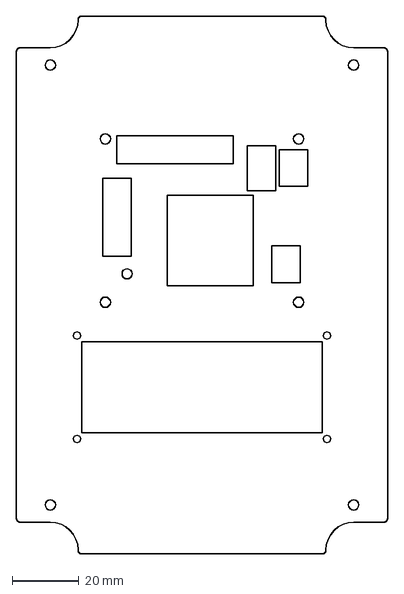
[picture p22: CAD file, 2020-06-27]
Hardware/Enclosures/TinkerAccess_Faceplate_Vertical.dxf
111.4 x 161.4 mm

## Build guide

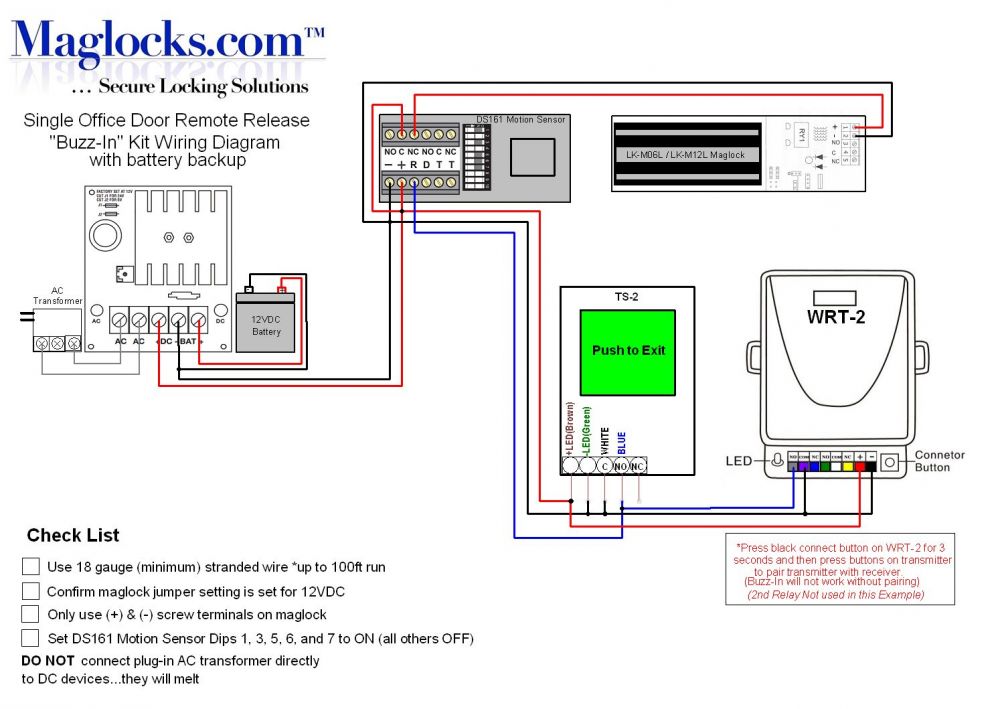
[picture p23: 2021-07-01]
Hardware/Implementations/w_bay_door/datasheets/maglock_wiring_diagram.jpg

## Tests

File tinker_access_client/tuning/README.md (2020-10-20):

# Current Sense Tuning

One of the features of the [custom tinkerAccess PCB](/Hardware/) is an input for a current transformer to detect the load current of the machine. The comparator circuitry on the PCB will prevent the tinkerAccess client from disabling power immediately to the machine, until the load current falls below a set threshold. The comparator threshold is set to discern between device 'running' current and device 'idle' current. On the original PCB designs, the threshold was set by changing resistor values on the PCB. On newer designs, the threshold can be set programmatically via a PWM output of the Pi.

This guide covers the procedure to tune the programmable current threshold on newer PCB designs, and explains the config parameters involved in the process.

### Config Parameters

The first two parameters apply to both versions of PCBs, the programmable threshold and the threshold set by resistor values.

- __max_power_down_timeout__:[integer seconds] (default: Infinite)

  This parameter determines the number of seconds to wait for the current to fall below the threshold during logout/shutdown. Basically, it waits until the machine reaches an idle state before disabling power. If this parameter is not set, the default is that it will wait forever for the current to fall below the threshold. However in reality, if no current transformer is connected, the detected current will be zero and likely always be below the threshold. If current detection is not desired, to guarantee that the client does not get stuck in an infinite wait state waiting for the threshold detection, this parameter should be set to 0, which essentially disables the current detection. If a current transformer is connected and current detection is desired, this value should be set to the maximum number of seconds to wait for the device to go to an idle current state during logout/shutdown.

- __logout_coast_time__:[integer seconds] (default: 0)

  This parameter determines the number of seconds to wait for the machine to coast down during a logout/shutdown. During a logout/shutdown event, the client will first wait for the current detection state to go 'idle' or it will wait the max_power_down_timeout, whichever comes first. At this point, it determines the machine is in an idle state and will wait an additional number of seconds determined by this parameter, before disabling power to the machine. This logout coast time will give an additional few seconds for things like a spinning blade to coast to a stop, before actually disabling power. The default value is 0 seconds, or no wait. If a coast time is desired, this parameter should be set to value greater than 0 seconds.

These parameters apply to the PCBs with a programmable current threshold

- __use_pgm_current_threshold__:[True|False] (default: False)

  This parameter determines whether the programmable current detect threshold PWM output is used or not. For PCBs without a programmable threshold, this parameter should be False, therefore it can be ignored since the default is False. For PCBs with a programmable threshold, but applications where current detection is not desired, this parameter should also be set to False. In this case, the programmable threshold is set to its maximum value and should always be in the 'idle' detection state. For applications that require current detection with a PCB that has a programmable threshold, this parameter should be set to True and the remaining parameters are also enabled.

- __current_detect_setting__:[integer RMS milliamps] (default: 10000)

  This parameter is used to set the programmable current detection threshold. It is defined as RMS milliamps. It should be set between the measured 'idle' current and 'running' current. There is a maximum threshold current that is determined by the CT burden resistor and CT turns ratio. The tuning script will report the maximum programmable threshold. The tuning script can also be ran at both 'idle' and 'running' conditions to determine the optimal threshold setting.

- __ct_burden_resistor__:[integer ohms] (default: 1000)

  This parameter is used in internal calculations and should match the actual value of the current transformer burden resistor on the PCB. The PCBs are built with a default burden resistor value of 1K. Should the range of the programmable threshold not be adequate, the burden resistor can be increased to decrease the range, and decreased to increase the range. If the physical resistor is changed, then this parameter should be modified to reflect that change.

- __ct_turns_ratio__:[integer turns ratio] (default: 2000)

  This parameter is used in internal calculations and should match the actual turns ratio of the current transformer connected to the PCB. If the recommended SparkFun SEN-11005 current transformer is used, then the default CT ratio of 2000:1 is correct. Should the range of the programmable threshold not be adequate, the CT ratio can be increased to decrease the range, and decreased to increase the range. If the physical CT is changed, then this parameter should be modified to reflect that change.

### Tuning script

The `tune_current_sense.py` Python script can be used on a running client to sweep the programmable current detection threshold to 'measure' the actual machine current under different conditions. If this script is run at 'idle' and then under 'running' conditions, the optimal programmable threshold level will be somewhere between these two values.

Below is the procedure for running the the tuning script:

1. Edit the `/etc/tinker-access-client.conf` file to ensure the programmable current threshold is enabled and CT parameters are correct.

   The programmable current threshold detection needs to be enabled before running the tuning script. In addition the CT burden resistor and turns ratio values need to match the actual hardware. If the standard resistor and CT is being used then the default values do not need to be modified. The initial current detection setting does not matter during the tuning process.
   ```
   use_pgm_current_threshold:True
   #current_detect_setting:10000
   #ct_burden_resistor:1000
   #ct_turns_ratio:2000
   ```

   Restart the tinker-access-client and ensure it is running if changes are made to the config file.

2. Edit the `tune_current_sense.py` file to make sure the parameters match the client configuration.

   The following parameters in the script need to match the client config file and setup before running:
   ```
   pin_current_detect = 12     # GPIO pin number of the current detect input
   pin_current_threshold = 18  # GPIO pin number of the current threshold PWM output
   Rb = 1000                   # Burden resistor value on the PCB
   turns = 2000                # Turns ratio of current transformer
   Vcc = 3.3                   # GPIO voltage
   ```

3. Run the tuning script at machine idle conditions.

   With the machine at an idle condition, run the tuning script. The script will sweep all programmable threshold values. Record the current threshold value, where the detector transitions. Run the script with the following command:
   ```
   python tune_current_sense.py
   ```

   In this example, the partial output looks like this:
   ```
   Sweeping the current threshold PWM duty cycle, 50 steps in total, the current duty cycle setting is: 50
   Current sense setting: PWM Duty Cycle:  50 (100.0%), PWM Output: 3.300 Volts, Current Threshold Setting:  4.67 Amps(RMS), Detector: 0
   Current sense setting: PWM Duty Cycle:  49 ( 98.0%), PWM Output: 3.234 Volts, Current Threshold Setting:  4.57 Amps(RMS), Detector: 0
   Current sense setting: PWM Duty Cycle:  48 ( 96.0%), PWM Output: 3.168 Volts, Current Threshold Setting:  4.48 Amps(RMS), Detector: 0
   Current sense setting: PWM Duty Cycle:  47 ( 94.0%), PWM Output: 3.102 Volts, Current Threshold Setting:  4.39 Amps(RMS), Detector: 0
   ...
   Current sense setting: PWM Duty Cycle:   3 (  6.0%), PWM Output: 0.198 Volts, Current Threshold Setting:  0.28 Amps(RMS), Detector: 0
   Current sense setting: PWM Duty Cycle:   2 (  4.0%), PWM Output: 0.132 Volts, Current Threshold Setting:  0.19 Amps(RMS), Detector: 0
   Current sense setting: PWM Duty Cycle:   1 (  2.0%), PWM Output: 0.066 Volts, Current Threshold Setting:  0.09 Amps(RMS), Detector: 0
   Current sense setting: PWM Duty Cycle:   0 (  0.0%), PWM Output: 0.000 Volts, Current Threshold Setting:  0.00 Amps(RMS), Detector: 1
   Resetting PWM duty cycle to 50
   ```

   The first thing to note is that the maximum current threshold setting is 4.67 Amps. If this is not adequate for your application, then the CT burden resistor or CT turns ratio will need to be replaced in order to change the range. Second, the detector triggers at 0 Amps, therefore in this application, the 'idle' current is 0.

4. Rerun the tuning script with the machine running.

   Start the machine in its typical minimum running current condition. This could be the machine is on, but not being subjected to any load.

   In this example, the partial output looks like this:
   ```
   Sweeping the current threshold PWM duty cycle, 50 steps in total, the current duty cycle setting is: 50
   Current sense setting: PWM Duty Cycle:  50 (100.0%), PWM Output: 3.300 Volts, Current Threshold Setting:  4.67 Amps(RMS), Detector: 0
   Current sense setting: PWM Duty Cycle:  49 ( 98.0%), PWM Output: 3.234 Volts, Current Threshold Setting:  4.57 Amps(RMS), Detector: 0
   ...
   Current sense setting: PWM Duty Cycle:  35 ( 70.0%), PWM Output: 2.310 Volts, Current Threshold Setting:  3.27 Amps(RMS), Detector: 0
   Current sense setting: PWM Duty Cycle:  34 ( 68.0%), PWM Output: 2.244 Volts, Current Threshold Setting:  3.17 Amps(RMS), Detector: 0
   Current sense setting: PWM Duty Cycle:  33 ( 66.0%), PWM Output: 2.178 Volts, Current Threshold Setting:  3.08 Amps(RMS), Detector: 0
   Current sense setting: PWM Duty Cycle:  32 ( 64.0%), PWM Output: 2.112 Volts, Current Threshold Setting:  2.99 Amps(RMS), Detector: 0
   Current sense setting: PWM Duty Cycle:  31 ( 62.0%), PWM Output: 2.046 Volts, Current Threshold Setting:  2.89 Amps(RMS), Detector: 0
   Current sense setting: PWM Duty Cycle:  30 ( 60.0%), PWM Output: 1.980 Volts, Current Threshold Setting:  2.80 Amps(RMS), Detector: 1
   Current sense setting: PWM Duty Cycle:  29 ( 58.0%), PWM Output: 1.914 Volts, Current Threshold Setting:  2.71 Amps(RMS), Detector: 1
   Current sense setting: PWM Duty Cycle:  28 ( 56.0%), PWM Output: 1.848 Volts, Current Threshold Setting:  2.61 Amps(RMS), Detector: 1
   Current sense setting: PWM Duty Cycle:  27 ( 54.0%), PWM Output: 1.782 Volts, Current Threshold Setting:  2.52 Amps(RMS), Detector: 1
   Current sense setting: PWM Duty Cycle:  26 ( 52.0%), PWM Output: 1.716 Volts, Current Threshold Setting:  2.43 Amps(RMS), Detector: 1
   ...
   Current sense setting: PWM Duty Cycle:   1 (  2.0%), PWM Output: 0.066 Volts, Current Threshold Setting:  0.09 Amps(RMS), Detector: 1
   Current sense setting: PWM Duty Cycle:   0 (  0.0%), PWM Output: 0.000 Volts, Current Threshold Setting:  0.00 Amps(RMS), Detector: 1
   Resetting PWM duty cycle to 50
   ```

   In this example, the detector triggers at 2.80 Amps, therefore in this example, the 'running' current is 2.80 Amps.

5. Set the programmable threshold in the config file and restart the client.

   In the example above, the idle current is 0 and the running current is 2.80 Amps. A good threshold value would be half way between at 1.40 Amps. Since the config file value is in milliamps, the value should be 1400. The config file parameters would need to be modified to look like the following. Notice the CT parameters can be left commented out since we are using the default values:
   ```
   use_pgm_current_threshold:True
   current_detect_setting:1400
   #ct_burden_resistor:1000
   #ct_turns_ratio:2000
   ```

   After saving the config file, restart the tinker-access-client for the new parameter to take effect.

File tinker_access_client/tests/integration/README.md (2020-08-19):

# Integration Testing

These test use a custom [VirtualDevice](utils/VirtualDevice.py) fixture which replaces the GPIO library at runtime, so the pin state is stored in memory.   

The advantage of this is the test can be written and run in an environment where GPIO won't load 
(i.e. the build server of a development pc)

Example:

```
    def test_login(self):
        with tempfile.TemporaryDirectory() as temp_dir:
            opts = get_default_opts(temp_dir)
            with patch.object(requests, 'get') as mock_get, VirtualDevice(opts) as device:

                expected_transitions = [
                    State.INITIALIZED,
                    State.IDLE
                ]  

                # Assert that the device has initialized and is idle
                self.assertTransitions(device, expected_transitions)
                self.assertIdlePins(opts, device)  

                # Assert that a valid login causes the device to transition to in_use and enables the expected pins.
                mock_get.return_value = valid_login_response
                device.scan_badge('some_badge_code')
                expected_transitions.append(State.IN_USE)
                self.assertTransitions(device, expected_transitions)
                self.assertInUsePins(opts, device)

```

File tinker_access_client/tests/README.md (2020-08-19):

# Testing

To run tests, we can simply do:
```
python setup.py test
```

The Setup tools will take care of installing dependencies (i.e. nose, mock) and running the test suite.

## Unit Testing

Additional information regarding the unit test can be found [here](unit/README.md).

## Integration Testing

Additional information regarding the integration test can be found [here](integration/README.md).

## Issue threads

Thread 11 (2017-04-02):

Current Sense/Coastdown Time not implemented correctly.

eztinkerdreams, 2017-04-02:
On the SawStop if the user presses the logout button, while the power is on, they should be forced to disable power before the logout is completed. There should also be a logout coast time enforced after the user disables power, to allow for the blade to spin down.

eztinkerdreams, 2017-05-11:
Fixed, and confirmed by @RonaldThomas

Closed 2017-05-11.

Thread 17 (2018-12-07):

Unlock Time Incompatible with Door Access Solenoids

RonaldThomas, 2018-12-07:
1) The smallest unit of time the software considers for granting access is one minute and I'm pretty sure it's stored as an integer. We want to be able to specify time in seconds.
2) IIRC, the refactor of the client software began retrieving the access time granted for each badge in event from the deviceAccess table in the SQL database on the server. The records in deviceAccess are unique combinations of users and devices which are created when a trainer gives someone access to a device. Currently, the server software automatically populates the time field for each record with "100" when the record is created. If we want the access time to be specified for each user in deviceAccess, we should change server.py to pull in the time value as a variable from somewhere instead of as a hard-coded value.

ToddFranks-TM, 2020-12-10:
PR #44 addresses this issue. Instead of modifying the server side to send the time value, this is handled as a special "door" parameter on the client to set the access time and ignore the server value sent.

ToddFranks-TM, 2021-09-21:
This issue has been addressed, so I am closing

Closed 2021-09-21.

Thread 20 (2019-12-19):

Incorrect Footprint for U$2

RonaldThomas, 2019-12-19:
The board design currently has the footprint for U$2 specified as SOT-23-5, when it should be the slightly smaller SC-70-5.

Closed 2020-06-27.

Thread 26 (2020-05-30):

No Exception Handling Around I2C Communications

RonaldThomas, 2020-05-30:
With some frequency, the TinkerAccess node that we have installed on the Laser Cutter seems to be crashing and a full hardware restart is required to recover. Checking syslog on that device shows errors like these:

`pi@lasercutterpi:~ $ cat /var/log/syslog.1 | grep Errno
May 20 12:08:58 lasercutterpi [Errno 121] Remote I/O error tinker-access-client (2017.07.19.18) 4 Laser Cutter - RDWorks 210 Ron Thomas 150060E726B4
Traceback (most recent call last):
  File "/usr/local/lib/python2.7/dist-packages/tinker_access_client/DeviceApi.py", line 242, in write self.__write_to_lcd(first_line, second_line)
  File "/usr/local/lib/python2.7/dist-packages/tinker_access_client/DeviceApi.py", line 129, in __write_to_lcd lcd.write(first_line, second_line)
  File "/usr/local/lib/python2.7/dist-packages/tinker_access_client/LcdApi.py", line 179, in write self.lcd_display_string(first_line, 1, 0)
  File "/usr/local/lib/python2.7/dist-packages/tinker_access_client/LcdApi.py", line 156, in lcd_display_string self.lcd_write(ord(char), Rs)
  File "/usr/local/lib/python2.7/dist-packages/tinker_access_client/LcdApi.py", line 122, in lcd_write self.lcd_write_four_bits(mode | ((cmd << 4) & 0xF0))
  File "/usr/local/lib/python2.7/dist-packages/tinker_access_client/LcdApi.py", line 126, in lcd_write_four_bits self.lcd_device.write_cmd(data | LCD_BACKLIGHT)
  File "/usr/local/lib/python2.7/dist-packages/tinker_access_client/I2CApi.py", line 46, in write_cmd self.bus.write_byte_data(self.addr, cmd, 0)
  File "/usr/local/lib/python2.7/dist-packages/smbus2/smbus2.py", line 204, in write_byte_data ioctl(self.fd, I2C_SMBUS, msg)
IOError: [Errno 121] Remote I/O error
May 20 12:09:15 lasercutterpi [Errno 121] Remote I/O error tinker-access-client (2017.07.19.18) 4 Laser Cutter - RDWorks 210 Ron Thomas 150060E726B4
Traceback (most recent call last):
  File "/usr/local/lib/python2.7/dist-packages/tinker_access_client/DeviceApi.py", line 242, in write self.__write_to_lcd(first_line, second_line)
  File "/usr/local/lib/python2.7/dist-packages/tinker_access_client/DeviceApi.py", line 128, in __write_to_lcd with LcdApi() as lcd:
  File "/usr/local/lib/python2.7/dist-packages/tinker_access_client/LcdApi.py", line 102, in __init__ self.__init__display()
  File "/usr/local/lib/python2.7/dist-packages/tinker_access_client/LcdApi.py", line 113, in __init__display self.lcd_write(LCD_FUNCTIONSET | LCD_2LINE | LCD_5x8DOTS | LCD_4BITMODE)
  File "/usr/local/lib/python2.7/dist-packages/tinker_access_client/LcdApi.py", line 122, in lcd_write self.lcd_write_four_bits(mode | ((cmd << 4) & 0xF0))
  File "/usr/local/lib/python2.7/dist-packages/tinker_access_client/LcdApi.py", line 126, in lcd_write_four_bits self.lcd_device.write_cmd(data | LCD_BACKLIGHT)
  File "/usr/local/lib/python2.7/dist-packages/tinker_access_client/I2CApi.py", line 46, in write_cmd self.bus.write_byte_data(self.addr, cmd, 0)
  File "/usr/local/lib/python2.7/dist-packages/smbus2/smbus2.py", line 204, in write_byte_data ioctl(self.fd, I2C_SMBUS, msg)
IOError: [Errno 121] Remote I/O error
May 20 12:09:29 lasercutterpi [Errno 121] Remote I/O error tinker-access-client (2017.07.19.18) 4
Traceback (most recent call last):
  File "/usr/local/lib/python2.7/dist-packages/tinker_access_client/DeviceApi.py", line 242, in write self.__write_to_lcd(first_line, second_line)
  File "/usr/local/lib/python2.7/dist-packages/tinker_access_client/DeviceApi.py", line 129, in __write_to_lcd lcd.write(first_line, second_line)
  File "/usr/local/lib/python2.7/dist-packages/tinker_access_client/LcdApi.py", line 179, in write self.lcd_display_string(first_line, 1, 0)
  File "/usr/local/lib/python2.7/dist-packages/tinker_access_client/LcdApi.py", line 156, in lcd_display_string self.lcd_write(ord(char), Rs)
  File "/usr/local/lib/python2.7/dist-packages/tinker_access_client/LcdApi.py", line 122, in lcd_write self.lcd_write_four_bits(mode | ((cmd << 4) & 0xF0))
  File "/usr/local/lib/python2.7/dist-packages/tinker_access_client/LcdApi.py", line 127, in lcd_write_four_bits self.lcd_strobe(data)
  File "/usr/local/lib/python2.7/dist-packages/tinker_access_client/LcdApi.py", line 131, in lcd_strobe self.lcd_device.write_cmd(data | En | LCD_BACKLIGHT)
  File "/usr/local/lib/python2.7/dist-packages/tinker_access_client/I2CApi.py", line 46, in write_cmd self.bus.write_byte_data(self.addr, cmd, 0)
  File "/usr/local/lib/python2.7/dist-packages/smbus2/smbus2.py", line 204, in write_byte_data ioctl(self.fd, I2C_SMBUS, msg)
IOError: [Errno 121] Remote I/O error
May 20 12:09:30 lasercutterpi [Errno 121] Remote I/O error tinker-access-client (2017.07.19.18) 4
Traceback (most recent call last):
  File "/usr/local/lib/python2.7/dist-packages/tinker_access_client/Client.py", line 593, in run client.wait()
  File "/usr/local/lib/python2.7/dist-packages/tinker_access_client/Client.py", line 500, in wait self.__device.wait()
  File "/usr/local/lib/python2.7/dist-packages/tinker_access_client/DeviceApi.py", line 261, in wait self.__raise_fault()
  File "/usr/local/lib/python2.7/dist-packages/tinker_access_client/DeviceApi.py", line 265, in __raise_fault raise self.__fault
IOError: [Errno 121] Remote I/O error`

While we haven't yet identified the ultimate root cause of the problem, it would be great to add exception handling to the relevant sections of the code so it could least make an attempt at self-recovery.

lucosmic, 2020-06-11:
I don't know if this is to be marked as a separate issue, but same thing happened when it couldn't connect to the TinkerMill WiFi, if I'm not mistaken.

RonaldThomas, 2020-06-11:
> I don't know if this is to be marked as a separate issue, but similar thing happened when it couldn't connect to the TinkerMill WiFi, if I'm not mistaken.

The WiFi connectivity problems are a separate issue and (we believe) unrelated to the TinkerAccess code.

lucosmic, 2020-06-11:
Yes connectivity problems may be unrelated to TinkerAccess, but I remember the TinkerAccess node not explicitly telling me on the LCD panel that it couldn't connect to the Wi-Fi, for users to help diagnose the problem. Anyway, I'm familiarizing myself with the code.

lttech-llc, 2020-06-27:
The new release v2020.06.27.23 has fixes for this issue. It captures any I2C bus errors and will retry 5 times before declaring a fatal error, forcing a reboot.

Closed 2020-06-27.

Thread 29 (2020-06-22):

Missing Ground Connection on I2C Isolator

RonaldThomas, 2020-06-22:
Pin 5 on device U1 (the I2C isolator) is floating and should be connected to GND.

lttech-llc, 2020-09-08:
Fixed in PCB rev 1.4.

Closed 2020-09-08.

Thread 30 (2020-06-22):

Pullup Resistors Needed for I2C Isolator

RonaldThomas, 2020-06-22:
From Todd Franks:

> I am able to get the LCD to work on J8 by adding 10k pullups to the J9 connector. So with nothing connected to J9 (no pullups) the isolator thinks the J9 side is driving, pulling the non-isolated side low and thus not allowing anything to work on the non-isolated side. The isolated side needs some default high value pullups so when nothing is connected, it will still work.

lttech-llc, 2020-09-08:
Fixed in PCB rev 1.4

Closed 2020-09-08.

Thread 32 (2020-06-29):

Inputs are 5V but Pi is not 5V Tolerant

lttech-llc, 2020-06-29:
The RFID RX, current sense circuit, and logout pushbutton all output 5V logic level to Raspberry Pi inputs. The Pi GPIO is 3.3V and is not 5V tolerant. This could lead to damage and reliability issues on the Pi.

lttech-llc, 2020-09-08:
Fixed in PCB rev 1.4

Closed 2020-09-08.

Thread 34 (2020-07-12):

Screw Terminals Too Tall

RonaldThomas, 2020-07-12:
The PCB designs so far have accommodated some screw terminals TinkerMill has happened to have on hand. Unfortunately, these terminals are rather tall and protrude higher than the top surface of the RFID module. It would be great if future PCB designs used something like ASSMAN WSW A-TB350TE02 ([DigiKey A-TB350-TE02-ND](https://www.digikey.com/product-detail/en/assmann-wsw-components/A-TB350-TE02/A-TB350-TE02-ND/4329406), [Sparkfun PRT-08084](https://www.sparkfun.com/products/8084)).

Datasheet: [ASS_4091_CO.pdf](https://github.com/TinkerMill/tinkerAccess/files/4907787/ASS_4091_CO.pdf)

lttech-llc, 2020-08-24:
We decided in the design review to not implement this change for now

lttech-llc, 2020-09-08:
Not changed in PCB rev 1.4

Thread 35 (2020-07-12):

New PCB won't boot with Raspberry Pi 2

lttech-llc, 2020-07-12:
The new PCB design will not boot when installed on a Raspberry Pi 2. On a Pi 2, if the SCL pin is held low at power-up, it will boot to safe mode. With the 3.3V enable functionality added, and the pulldown resistor on the 3.3V enable GPIO, the 3.3V regulator is off by default at power-up. With the I2C isolator powered off, the SCL pin gets pulled low, thereby preventing a normal boot on a Pi 2. The fix is to change 3.3V enable from a pulldown to a pullup to the Pi 3.3V supply. This makes the 3.3V regulator default state to be on at power-up and allows a normal boot. After the Pi is running, it can still power cycle the 3.3V regulator to effectively reset the connected I2C devices which I believe is the intent of the 3.3V enable. This change will also allow the LCD display to be powered during boot and also display error messages during fatal errors instead of going blank. We may never retrofit a new PCB to an existing Pi2 node, but wanted to document this issue, and propose a fix during the respin.

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

lttech-llc, 2020-09-08:
Fixed in PCB rev 1.4

Closed 2020-09-08.

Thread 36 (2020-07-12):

Add programmable threshold to current sense circuit

lttech-llc, 2020-07-12:
The current sense detection circuit on the existing PCB is tuned by swapping out resistors on the PCB. The threshold of the detector is non-linear to resistor value changes, so it cannot be calculated and can only be determined by simulation or experimentation by resoldering different value resistors and measuring on the PCB which makes the process difficult. I have come up with a design tweak to the existing design, that makes the threshold response linear to reference voltage changes. A crude reference voltage is created by a GPIO PWM output. Because the PWM is not a precision analog output, the calculations are not precise but they are fairly linear. I have modified the existing PCB with these changes and tested with new Python code and is very reliable. In addition, a Python script can be ran, sweeping the PWM output to detect the actual value of the measured current. This script can be ran at "idle" conditions and "running conditions to optimally tune the programmable threshold current.  I am proposing this change for a respin of the existing PCB.

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

lttech-llc, 2020-09-08:
Feature added in PCB rev 1.4

Closed 2020-09-08.

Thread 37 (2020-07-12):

PCB Respin

lttech-llc, 2020-07-12:
Collecting all the bug fixes and proposed enhancements in one place. The attached file is a markup of all of the proposed changes:

- Issue #29
- Issue #30
- Issue #32
- Issue #34
- Issue #35
- Issue #36
- Fix component values to match BOM
- Add bypass cap to isolator
- Add pulldown to relay FET

[TinkerAccess_markups.pdf](https://github.com/TinkerMill/tinkerAccess/files/4928314/TinkerAccess_markups.pdf)

lttech-llc, 2020-09-08:
All changes implemented in PCB rev 1.4 except for issue #34

Closed 2020-09-08.

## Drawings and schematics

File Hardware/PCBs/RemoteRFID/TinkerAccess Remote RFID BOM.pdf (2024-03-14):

## TinkerAccess Remote RFID v1.0 BOM

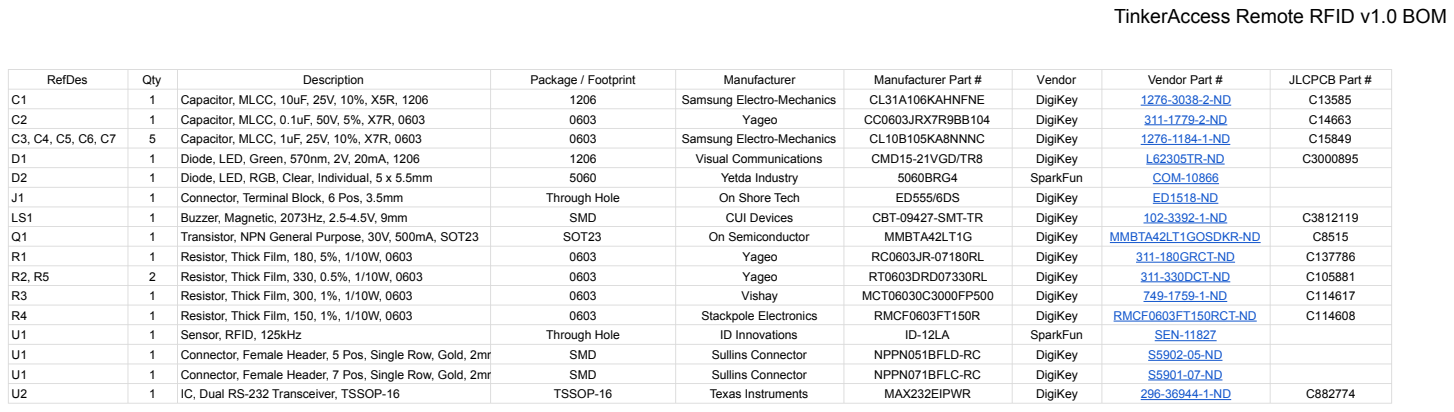
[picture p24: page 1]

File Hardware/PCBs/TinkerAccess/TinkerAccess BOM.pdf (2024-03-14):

# TinkerAccess v1.4 BOM

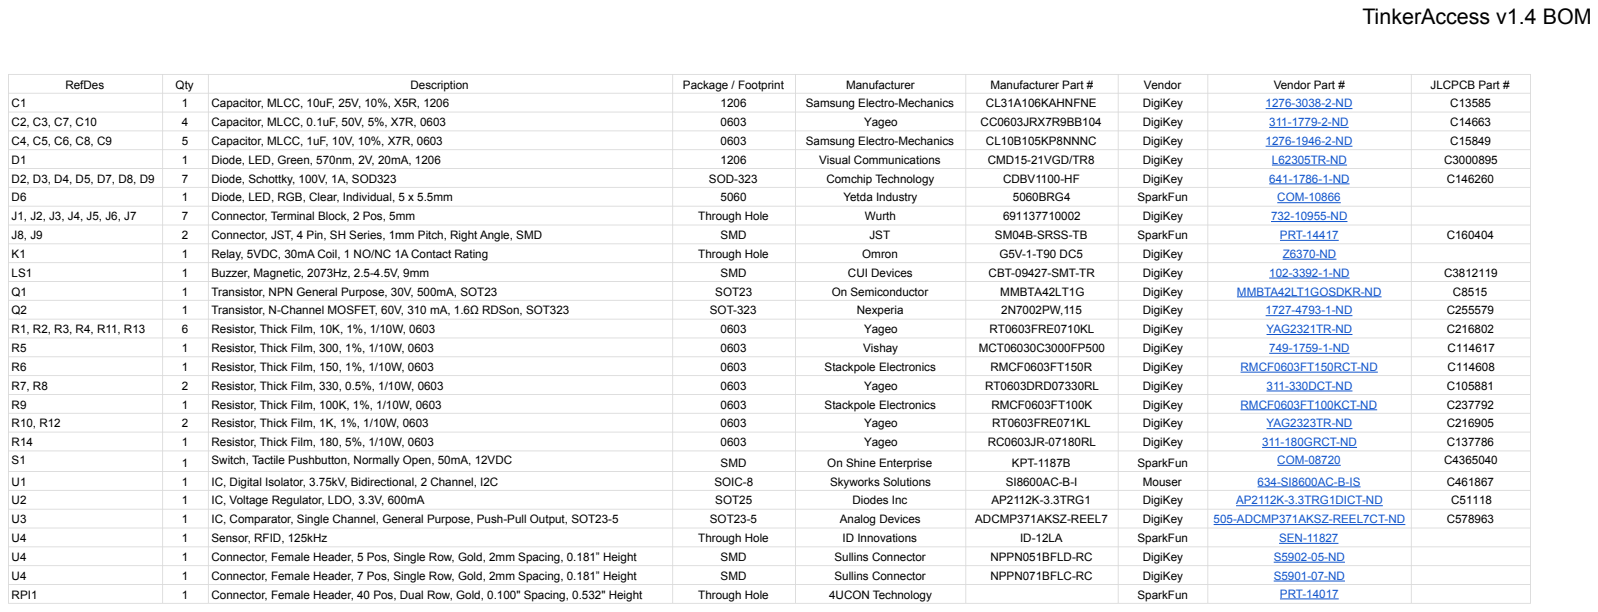
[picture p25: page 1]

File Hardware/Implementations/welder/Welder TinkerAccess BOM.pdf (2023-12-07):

# TinkerAccess Enclosure

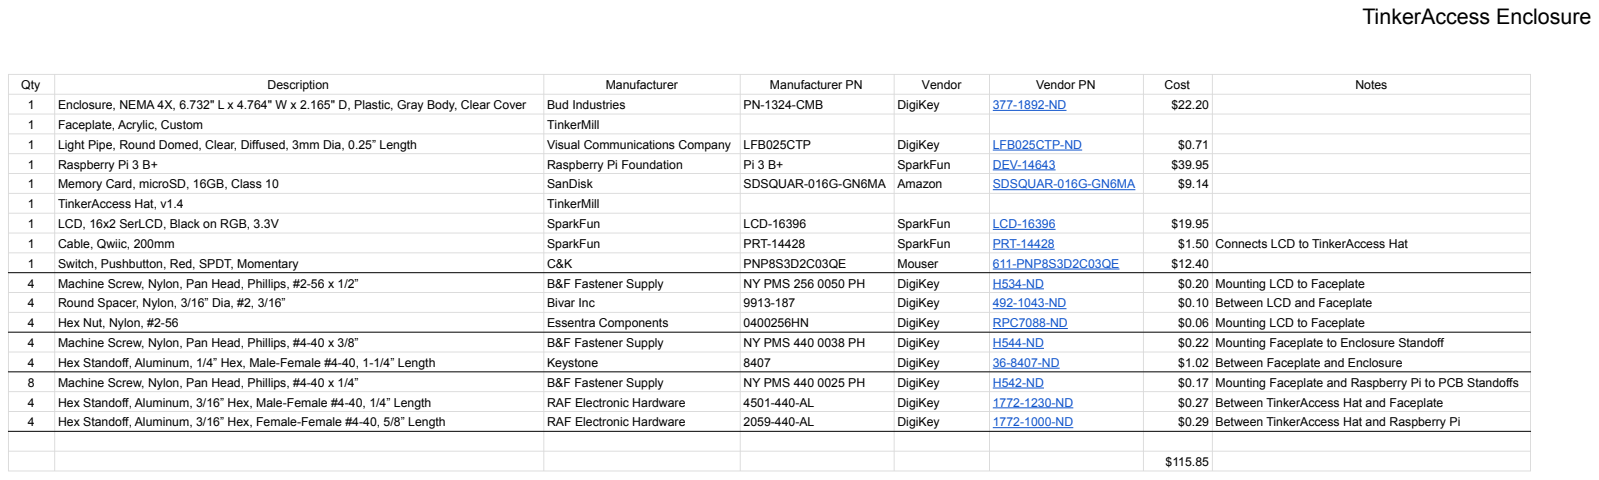
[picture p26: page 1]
Qty; Description; Manufacturer; Manufacturer PN; Vendor; Vendor PN; Cost; Notes; Enclosure, NEMA 4X, 6.732" L x 4.764" W x 2.165" D, Plastic, Gray Body, Clear Cover; Bud Industries; PN-1324-CMB; DigiKey; Faceplate, Acrylic, Custom; TinkerMill; Light Pipe, Round Domed, Clear, Diffused, 3mm Dia, 0.25” Length; Visual Communications Company LFB025CTP; LFB025CTP-ND; Raspberry Pi 3 B+; Raspberry Pi Foundation; SparkFun; DEV-14643; Memory Card, microSD, 16GB, Class 10; SanDisk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

# Contactor Enclosure

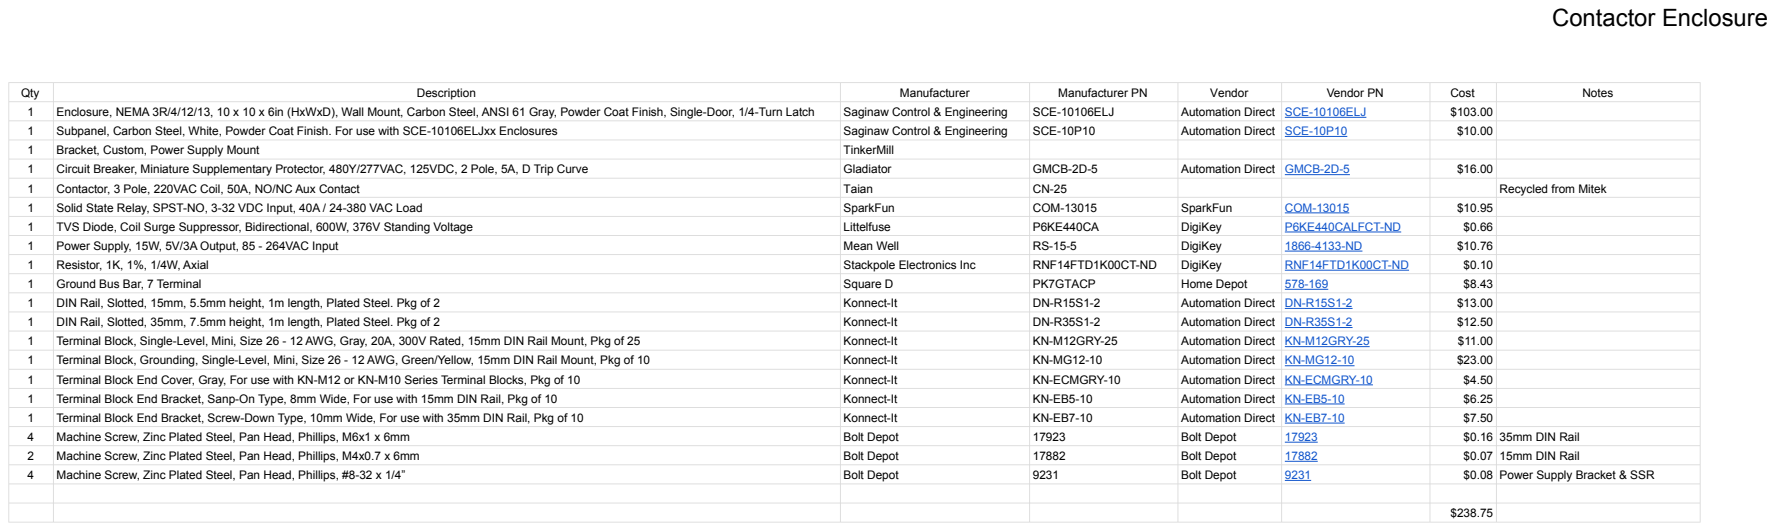
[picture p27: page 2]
Qty; Description; Manufacturer; Manufacturer PN; Vendor; Vendor PN; Cost; Notes; Enclosure, NEMA 3R/4/12/13, 10 x 10 x 6in (HxWxD), Wall Mount, Carbon Steel, ANSI 61 Gray, Powder Coat Finish, Single-Door, 1/4-Turn Latch; Saginaw Control & Engineering; SCE-10106ELJ; Automation Direct SCE-10106ELJ; Subpanel, Carbon Steel, White, Powder Coat Finish. For use with SCE-10106ELJxx Enclosures; SCE-10P10; Automation Direct SCE-10P10; Bracket, Custom, Power Supply Mount; TinkerMill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

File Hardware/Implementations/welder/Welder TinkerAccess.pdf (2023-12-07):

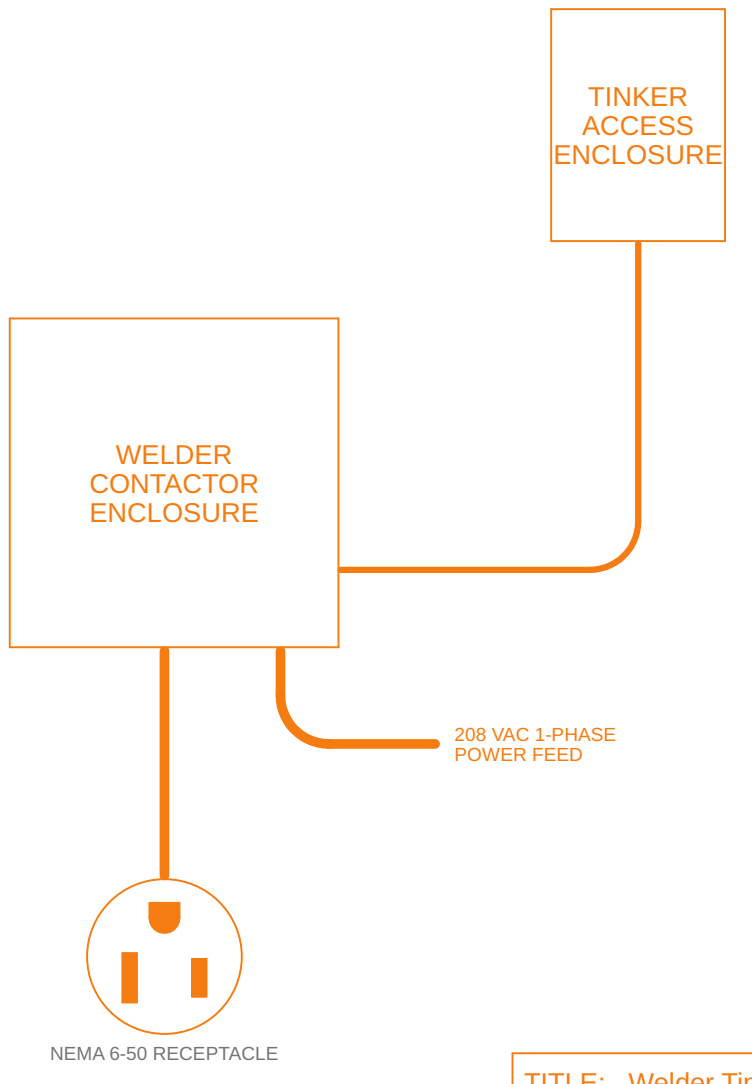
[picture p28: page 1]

Design by: | REV: 1.0

Date: 12/6/2023 8:25 PM | Sheet: 1/3

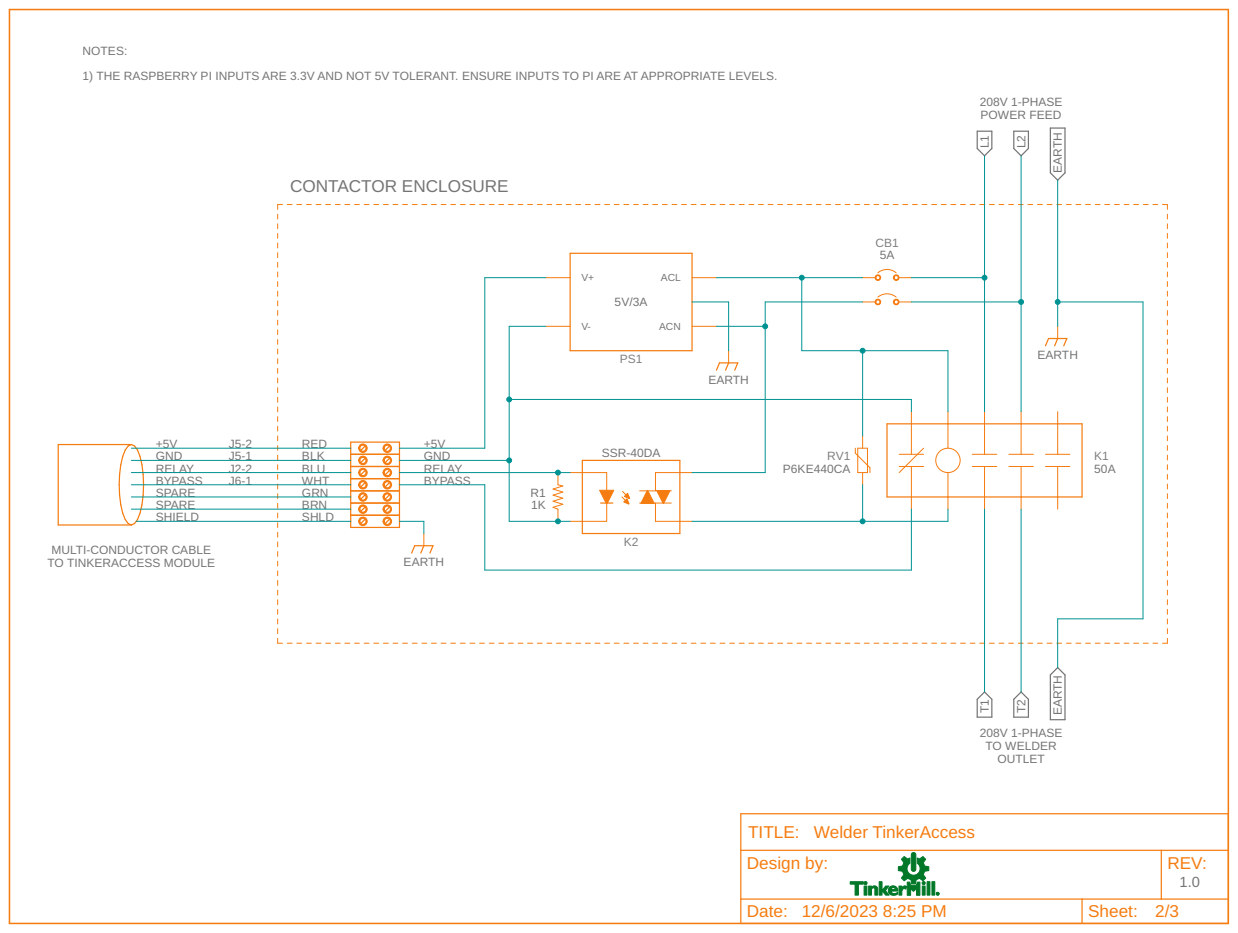
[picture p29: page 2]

NOTES: 1) THE RASPBERRY PI INPUTS ARE 3.3V AND NOT 5V TOLERANT. ENSURE INPUTS TO PI ARE AT APPROPRIATE LEVELS.

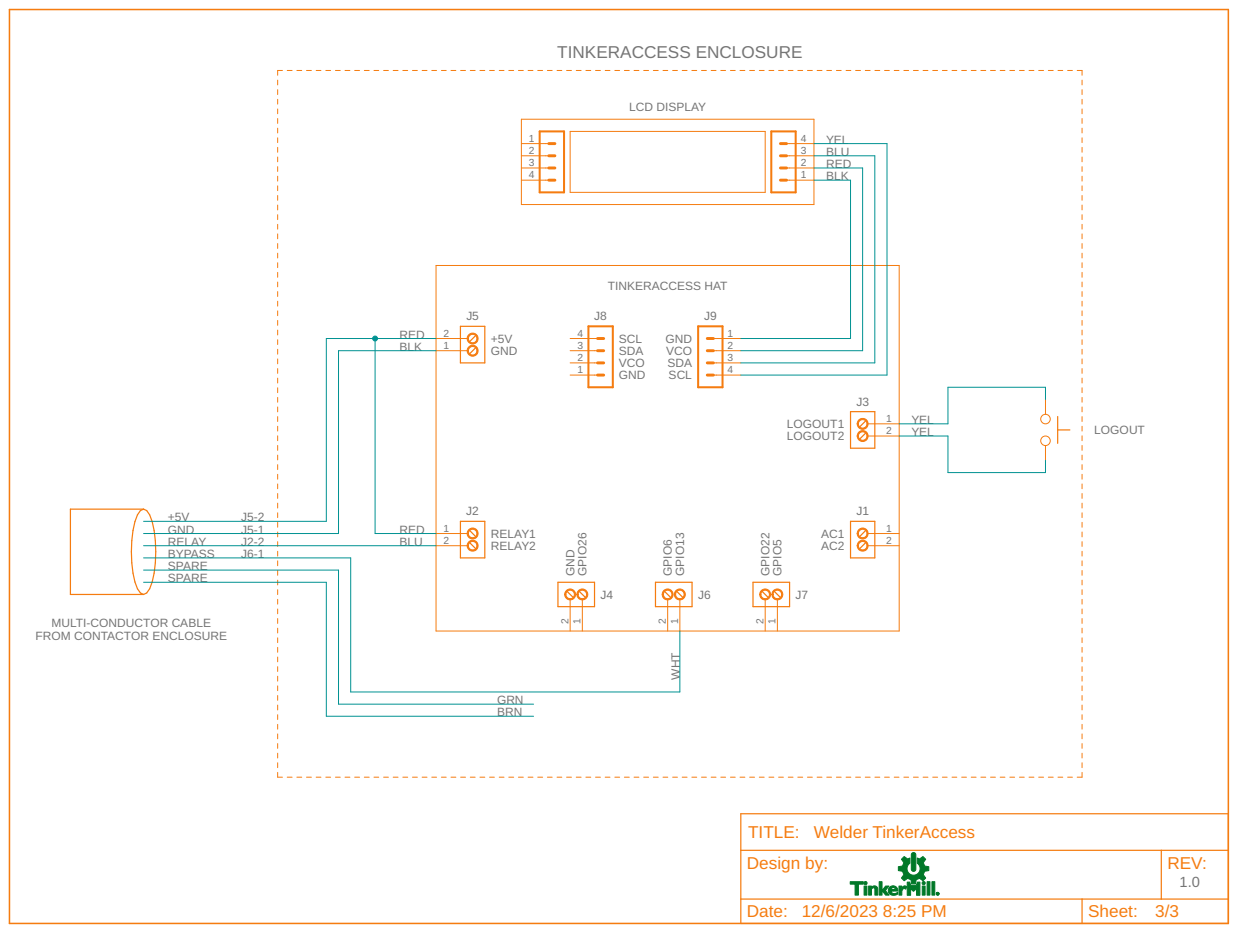
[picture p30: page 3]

3 | BLU
2 | RED
1 | BLK

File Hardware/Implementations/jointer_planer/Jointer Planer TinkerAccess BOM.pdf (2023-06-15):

## TinkerAccess Enclosure

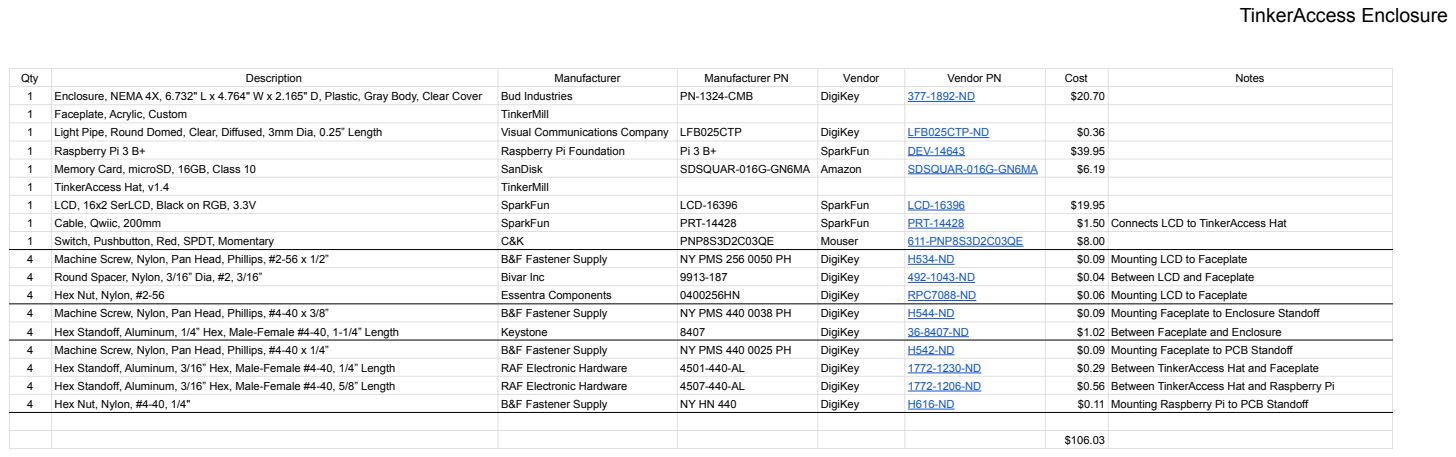
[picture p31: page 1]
Qty; Description; Manufacturer; Manufacturer PN; Vendor; Vendor PN; Cost; Notes; Enclosure, NEMA 4X, 6.732" L x 4.764" W x 2.165" D, Plastic, Gray Body, Clear Cover; Bud Industries; PN-1324-CMB; DigiKey; Faceplate, Acrylic, Custom; TinkerMill; Light Pipe, Round Domed, Clear, Diffused, 3mm Dia, 0.25” Length; Visual Communications Company LFB025CTP; LFB025CTP-ND; Raspberry Pi 3 B+; Raspberry Pi Foundation; SparkFun; DEV-14643; Memory Card, microSD, 16GB, Class 10; SanDisk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

## Contactor Enclosure

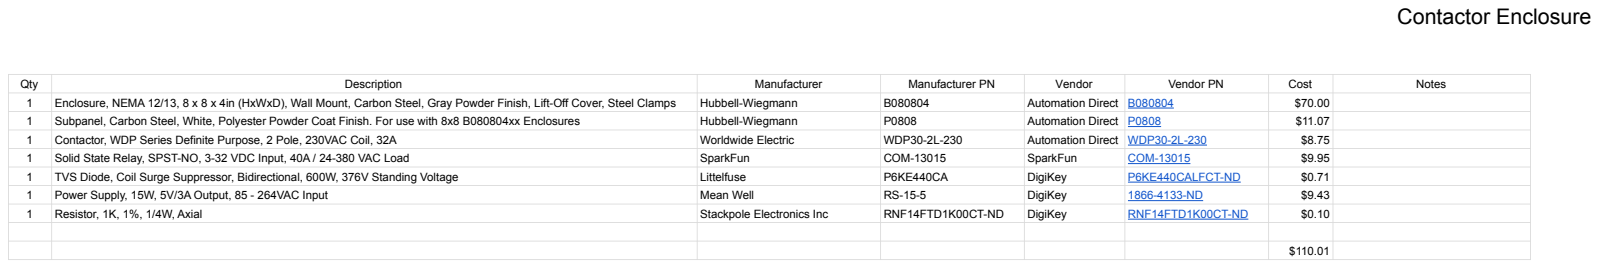
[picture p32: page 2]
Qty; Description; Manufacturer; Manufacturer PN; Vendor; Vendor PN; Cost; Notes; Enclosure, NEMA 12/13, 8 x 8 x 4in (HxWxD), Wall Mount, Carbon Steel, Gray Powder Finish, Lift-Off Cover, Steel Clamps; Hubbell-Wiegmann; Automation Direct B080804; Subpanel, Carbon Steel, White, Polyester Powder Coat Finish. For use with 8x8 B080804xx Enclosures; Automation Direct P0808; Contactor, WDP Series Definite Purpose, 2 Pole, 230VAC Coil, 32A; Worldwide Electric; WDP30-2L-230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

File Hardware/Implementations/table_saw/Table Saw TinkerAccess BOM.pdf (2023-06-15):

## TinkerAccess Enclosure

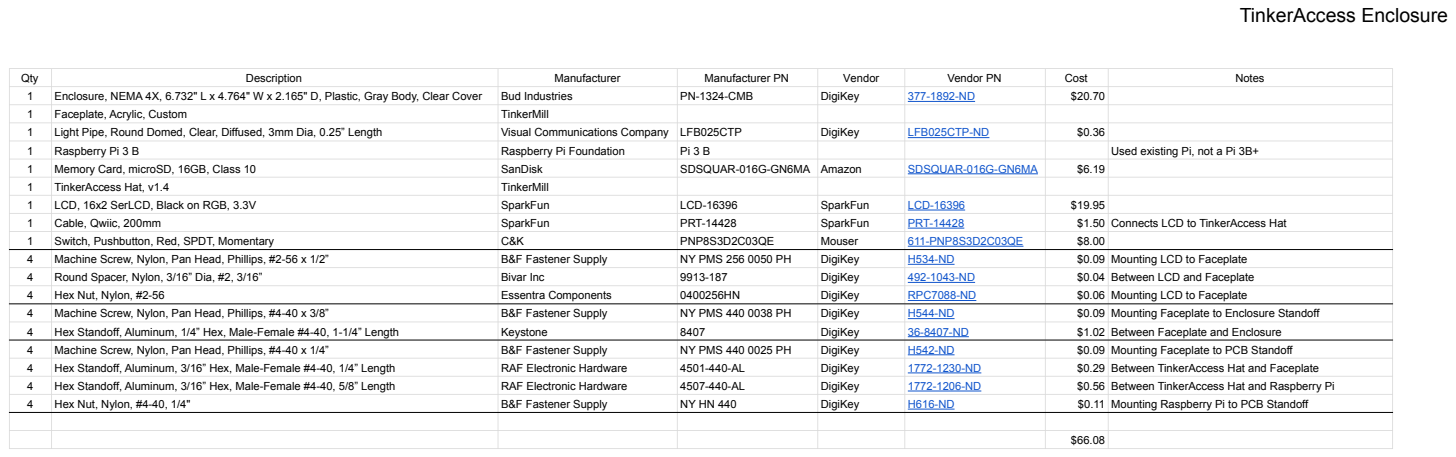
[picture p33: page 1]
Qty; Description; Manufacturer; Manufacturer PN; Vendor; Vendor PN; Cost; Notes; Enclosure, NEMA 4X, 6.732" L x 4.764" W x 2.165" D, Plastic, Gray Body, Clear Cover; Bud Industries; PN-1324-CMB; DigiKey; Faceplate, Acrylic, Custom; TinkerMill; Light Pipe, Round Domed, Clear, Diffused, 3mm Dia, 0.25” Length; Visual Communications Company LFB025CTP; LFB025CTP-ND; Raspberry Pi 3 B; Raspberry Pi Foundation; Used existing Pi, not a Pi 3B+; Memory Card, microSD, 16GB, Class 10; SanDisk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

## Contactor Enclosure

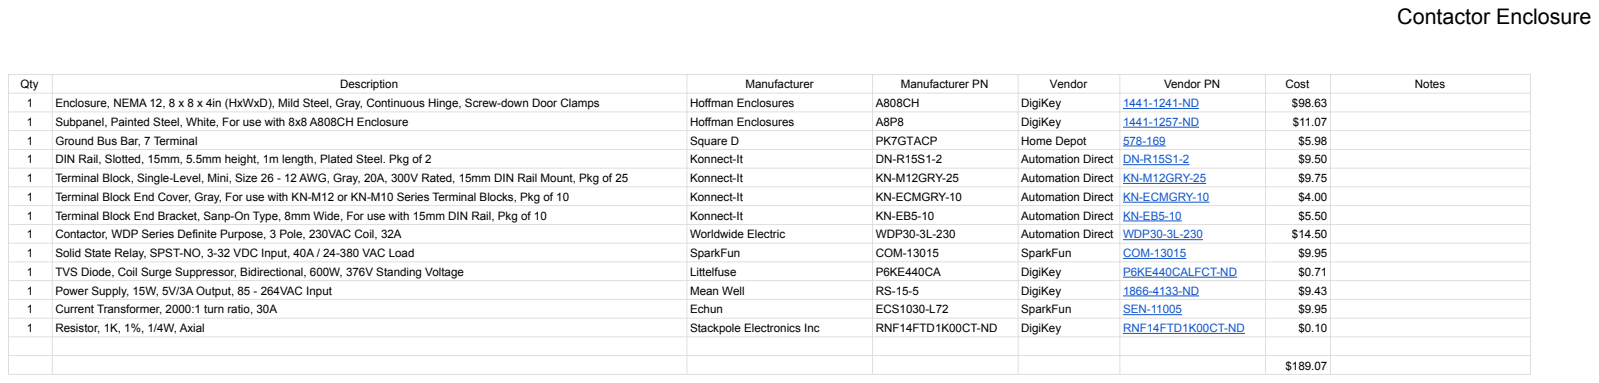
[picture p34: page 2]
Qty; Description; Manufacturer; Manufacturer PN; Vendor; Vendor PN; Cost; Notes; Enclosure, NEMA 12, 8 x 8 x 4in (HxWxD), Mild Steel, Gray, Continuous Hinge, Screw-down Door Clamps; Hoffman Enclosures; DigiKey; Subpanel, Painted Steel, White, For use with 8x8 A808CH Enclosure; Ground Bus Bar, 7 Terminal; Square D; PK7GTACP; Home Depot; DIN Rail, Slotted, 15mm, 5.5mm height, 1m length, Plated Steel. Pkg of 2; Konnect-It; Automation Direct DN-R15S1-2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

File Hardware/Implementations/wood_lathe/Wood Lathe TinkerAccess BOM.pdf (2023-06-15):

## TinkerAccess Enclosure

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

## Contactor Enclosure

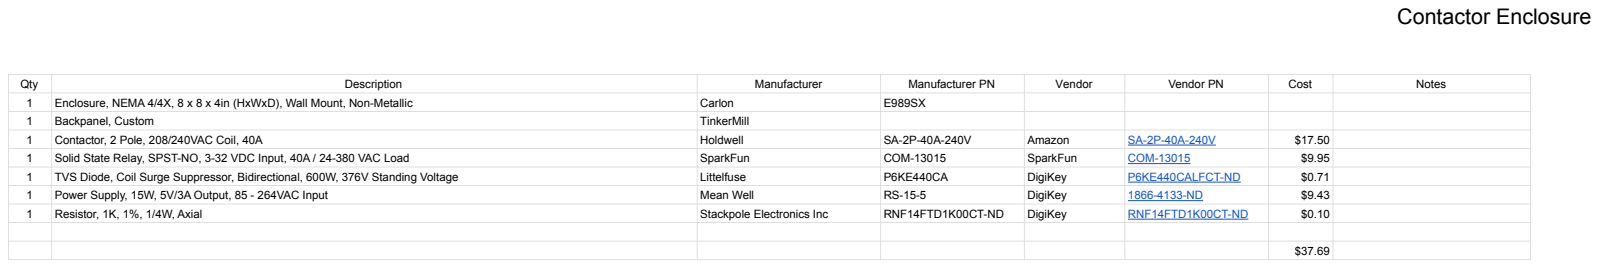
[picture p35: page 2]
Qty; Description; Manufacturer; Manufacturer PN; Vendor; Vendor PN; Cost; Notes; Enclosure, NEMA 4/4X, 8 x 8 x 4in (HxWxD), Wall Mount, Non-Metallic; Carlon; Backpanel, Custom; TinkerMill; Contactor, 2 Pole, 208/240VAC Coil, 40A; Holdwell; Amazon; Solid State Relay, SPST-NO, 3-32 VDC Input, 40A / 24-380 VAC Load; SparkFun; COM-13015; TVS Diode, Coil Surge Suppressor, Bidirectional, 600W, 376V Standing Voltage; Littelfuse; DigiKey; P6KE440CALFCT-ND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


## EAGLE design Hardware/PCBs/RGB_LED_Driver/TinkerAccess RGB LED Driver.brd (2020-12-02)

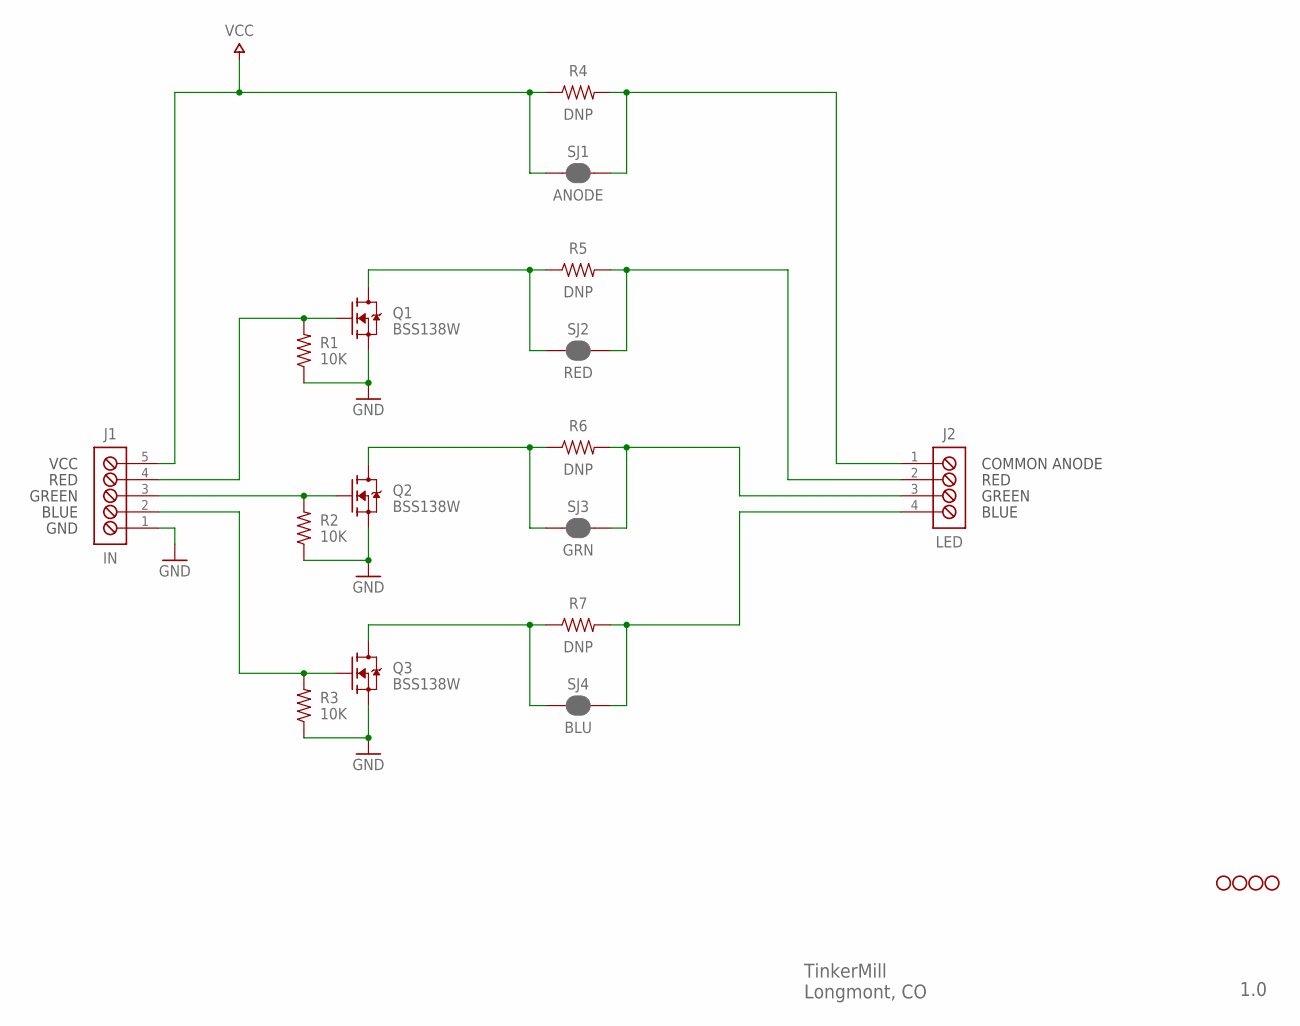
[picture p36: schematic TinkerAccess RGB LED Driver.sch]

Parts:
J1: IN; ON_SHORE_OSTVN05A150
J2: LED; ON_SHORE_OSTVN04A150
Q1, Q2, Q3: BSS138W; SOT323
R1, R2, R3: 10K; 0603
R4, R5, R6, R7: DNP; 0603
SJ1: ANODE; JMP_PAD_2X1_CLOSED_BY_PASTE
SJ2: RED; JMP_PAD_2X1_CLOSED_BY_PASTE
SJ3: GRN; JMP_PAD_2X1_CLOSED_BY_PASTE
SJ4: BLU; JMP_PAD_2X1_CLOSED_BY_PASTE
STANDOFF1, STANDOFF2, STANDOFF3, STANDOFF4: STANDOFF_2.3MM_NO_CU

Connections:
GND: J1.1, Q1.2 (S), Q2.2 (S), Q3.2 (S), R1.1, R2.1, R3.1
unnamed: J1.4, Q1.1 (G), R1.2
unnamed: J1.3, Q2.1 (G), R2.2
unnamed: J1.2, Q3.1 (G), R3.2
unnamed: J2.2, R5.2, SJ2.2
unnamed: J2.3, R6.2, SJ3.2
unnamed: J2.4, R7.2, SJ4.2
unnamed: Q1.3 (D), R5.1, SJ2.1
unnamed: Q2.3 (D), R6.1, SJ3.1
unnamed: Q3.3 (D), R7.1, SJ4.1
unnamed: J2.1, R4.2, SJ1.2
VCC: J1.5, R4.1, SJ1.1

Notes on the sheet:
VCC
RED
GREEN
BLUE
GND
COMMON ANODE
TinkerMill Longmont, CO
1.0

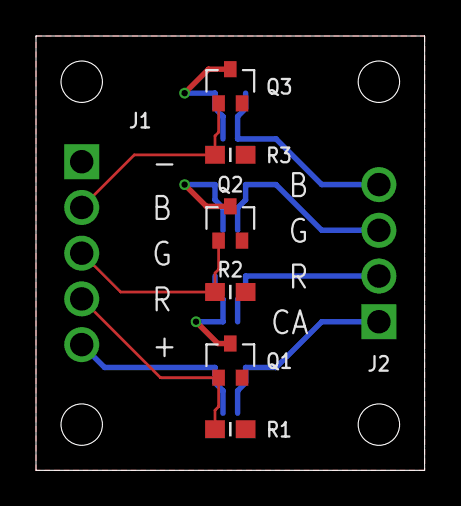
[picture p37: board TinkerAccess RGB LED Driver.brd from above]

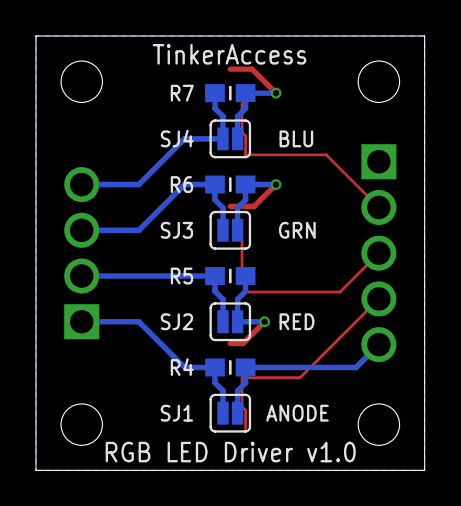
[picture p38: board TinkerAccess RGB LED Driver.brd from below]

Board: 2 copper layers, 21.6 x 24.1 mm, 20 parts (8 on the bottom side), 12 nets.

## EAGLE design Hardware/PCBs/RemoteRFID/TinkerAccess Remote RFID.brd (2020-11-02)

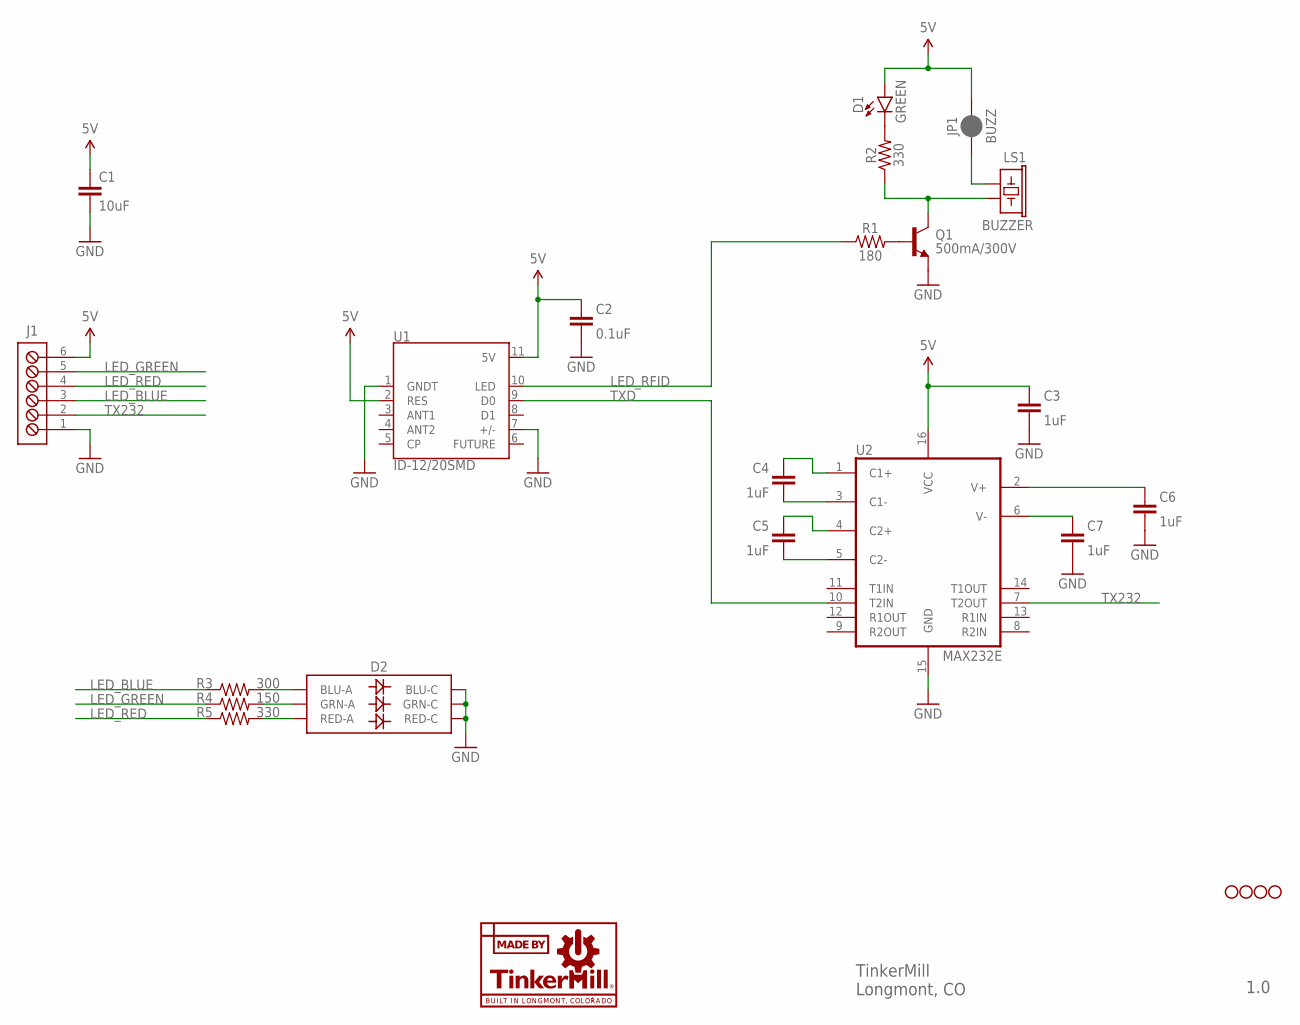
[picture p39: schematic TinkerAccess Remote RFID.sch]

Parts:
C1: 10uF; 1206
C2: 0.1uF; 0603
C3, C4, C5, C6, C7: 1uF; 0603
D1: GREEN; LED-1206
D2: LED-RGBNO_IC; LED-TRICOLOR-5050
J1: TB_6X1_TE_CONN_ED555_6DS; TE_CONN_ED555_6DS
JP1: BUZZ; SMT-JUMPER_2_NC_PASTE_NO-SILK
LOGO1: MADE_BY_TINKERMILL
LS1: BUZZER; BUZZER-CCV
Q1: 500mA/300V; SOT23-3
R1: 180; 0603
R2, R5: 330; 0603
R3: 300; 0603
R4: 150; 0603
STANDOFF1, STANDOFF2, STANDOFF3, STANDOFF4: STANDOFF_3.2MM_NO_CU_MASK
U1: ID-12/20SMD; ID-12_SMD
U2: MAX232E; TSSOP16

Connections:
5V: C1.1, C2.2, C3.2, D1.A, J1.6, JP1.2, U1.2 (RES), U1.11 (5V), U2.16 (VCC)
GND: C1.2, C2.1, C3.1, C6.1, C7.1, D2.4 (BLU-C), D2.5 (RED-C), D2.6 (GRN-C), J1.1, Q1.2 (E), U1.1 (GNDT), U1.7 (+/-), U2.15 (GND)
LED_BLUE: J1.3, R3.1
LED_GREEN: J1.5, R4.1
LED_RED: J1.4, R5.1
LED_RFID: R1.1, U1.10 (LED)
unnamed: Q1.1 (B), R1.2
unnamed: JP1.1, LS1.+ (1)
unnamed: LS1.- (2), Q1.3 (C), R2.1
unnamed: D1.C, R2.2
unnamed: C4.1, U2.3 (C1-)
unnamed: C4.2, U2.1 (C1+)
unnamed: C5.1, U2.5 (C2-)
unnamed: C5.2, U2.4 (C2+)
unnamed: D2.2 (RED-A), R5.2
unnamed: D2.1 (GRN-A), R4.2
unnamed: D2.3 (BLU-A), R3.2
unnamed: C6.2, U2.2 (V+)
unnamed: C7.2, U2.6 (V-)
TX232: J1.2, U2.7 (T2OUT)
TXD: U1.9 (D0), U2.10 (T2IN)

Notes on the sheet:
TinkerMill Longmont, CO
1.0

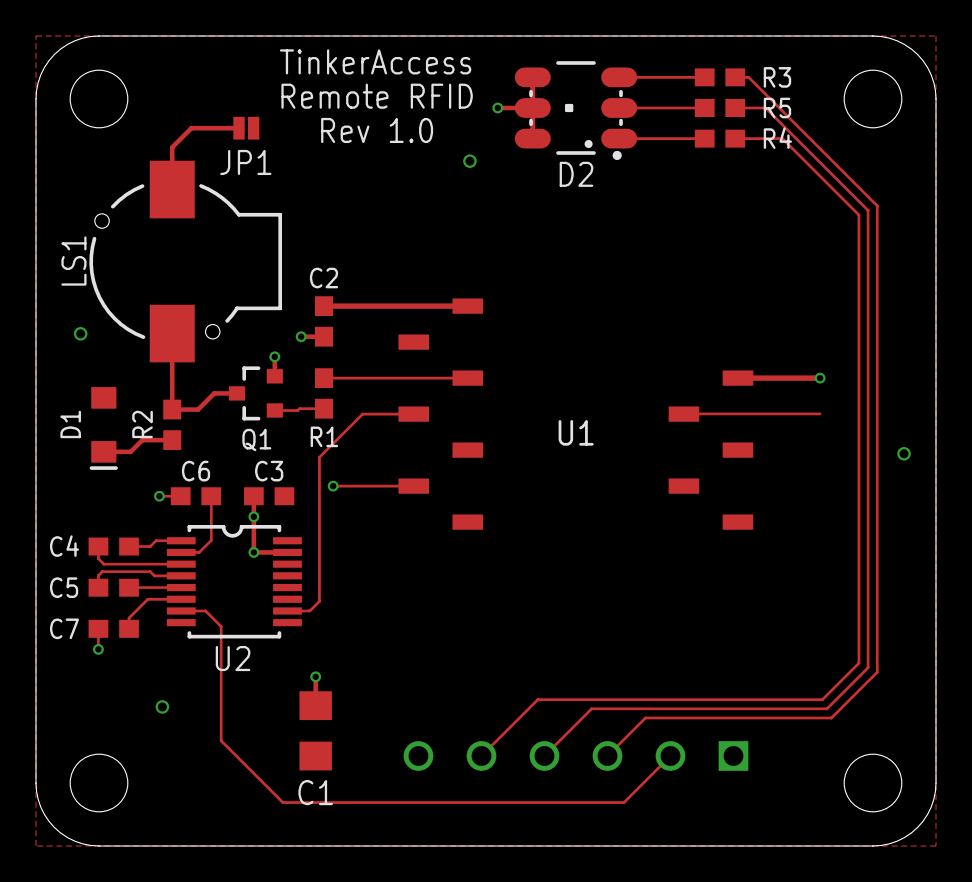
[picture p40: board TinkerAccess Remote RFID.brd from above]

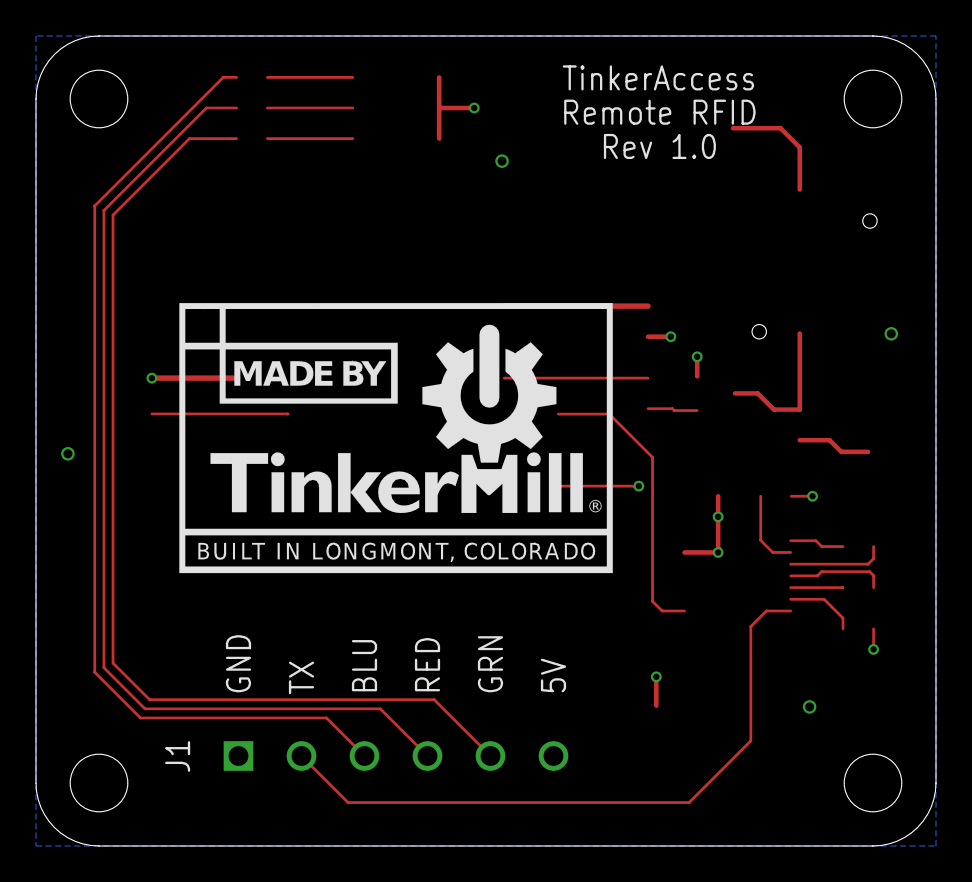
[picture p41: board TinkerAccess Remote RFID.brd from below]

Board: 2 copper layers, 50.0 x 45.0 mm, 25 parts (2 on the bottom side), 21 nets.

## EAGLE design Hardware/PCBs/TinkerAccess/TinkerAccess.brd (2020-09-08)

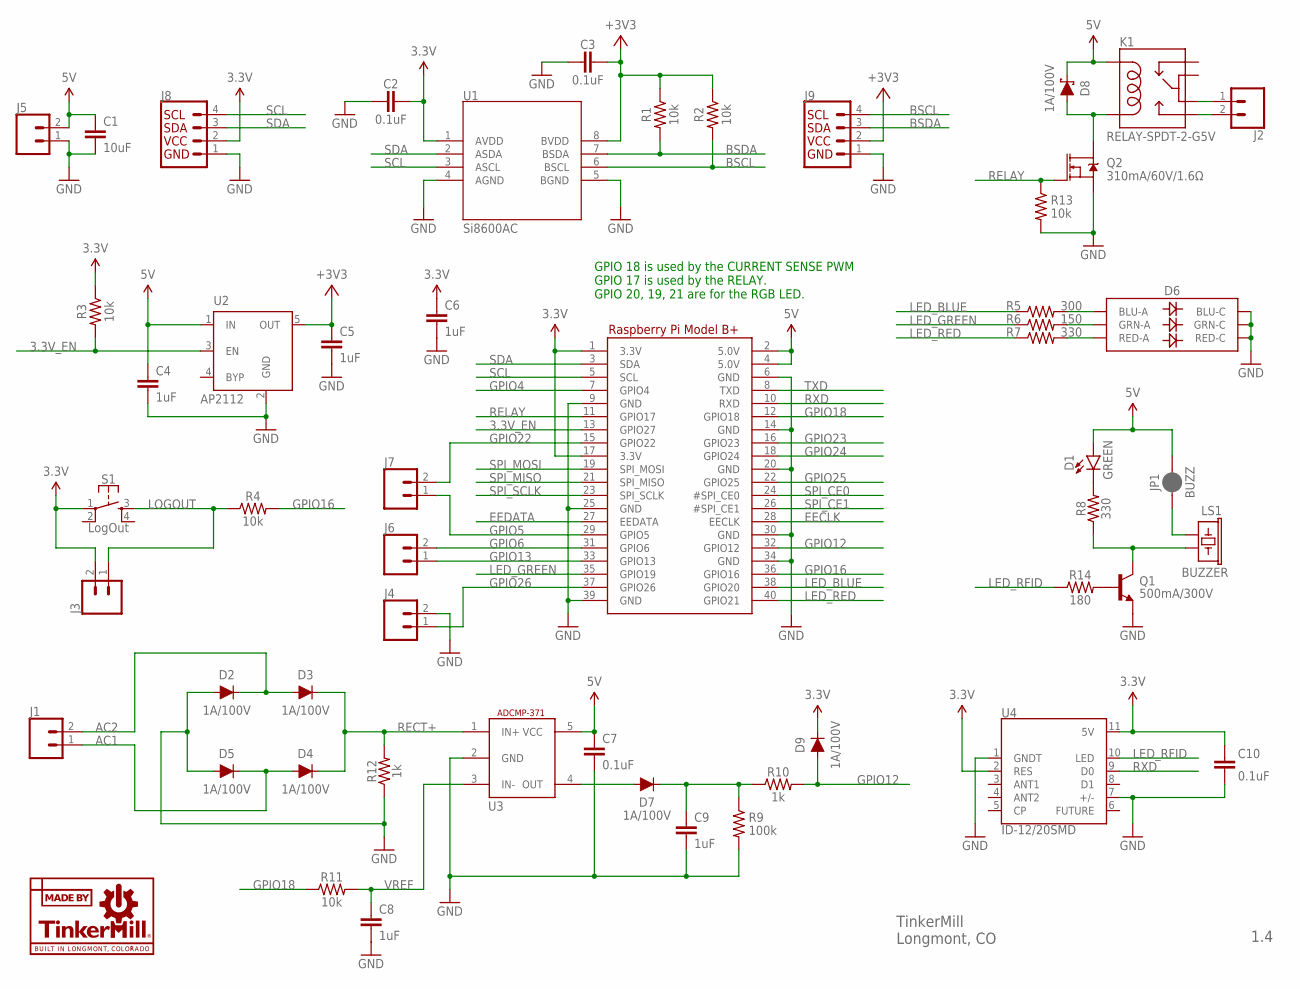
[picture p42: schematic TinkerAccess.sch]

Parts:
C1: 10uF; 1206
C2, C3, C7, C10: 0.1uF; 0603
C4, C5, C6, C8, C9: 1uF; 0603
D1: GREEN; LED-1206
D2, D3, D4, D5, D7, D8, D9: 1A/100V; SOD-323
D6: LED-RGBNO_IC; LED-TRICOLOR-5050
J1, J2, J3, J4, J5, J6, J7: CONN_025MM; SCREWTERMINAL-5MM-2
J8, J9: QWIIC_CONNECTORJS-1MM; 1X04_1MM_RA
JP1: BUZZ; SMT-JUMPER_2_NC_PASTE_NO-SILK
K1: RELAY-SPDT-2-G5V; RELAY-G5V
LOGO1: MADE_BY_TINKERMILL
LS1: BUZZER; BUZZER-CCV
Q1: 500mA/300V; SOT23-3
Q2: 310mA/60V/1.6Ω; SOT323
R1, R2, R3, R4, R11, R13: 10k; 0603
R5: 300; 0603
R6: 150; 0603
R7, R8: 330; 0603
R9: 100k; 0603
R10, R12: 1k; 0603
R14: 180; 0603
RPI1: RASPBERRYPI_BPLUS_HATNOSLOTS; PI_HAT_NOSLOTS
S1: LogOut; TACTILE_SWITCH_SMD_5.2MM
U1: Si8600AC; SOIC127P600X175-8
U2: AP2112; SOT23-5
U3: ADCMP-371; SC-70-5
U4: ID-12/20SMD; ID-12_SMD

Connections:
3.3V: C2.2, C6.1, C10.2, D9.C, J3.2, J8.2 (VCC), R3.1, RPI1.1 (3.3V), RPI1.17 (3.3V), S1.1, U1.1 (AVDD), U4.2 (RES), U4.11 (5V)
3.3V_EN: R3.2, RPI1.13 (GPIO27), U2.3 (EN)
5V: C1.1, C4.1, C7.1, D1.A, D8.C, J5.2, JP1.2, K1.2, RPI1.2 (5.0V), RPI1.4 (5.0V), U2.1 (IN), U3.5 (VCC)
+3V3: C3.2, C5.1, J9.2 (VCC), R1.1, R2.1, U1.8 (BVDD), U2.5 (OUT)
AC1: D4.A, D5.C, J1.1
AC2: D2.C, D3.A, J1.2
BSCL: J9.4 (SCL), R2.2, U1.6 (BSCL)
BSDA: J9.3 (SDA), R1.2, U1.7 (BSDA)
COMPOUT: D7.A, U3.4 (OUT)
DETECT: C9.1, D7.C, R9.1, R10.1
EECLK: RPI1.28 (EECLK)
EEDATA: RPI1.27 (EEDATA)
GND: C1.2, C2.1, C3.1, C4.2, C5.2, C6.2, C7.2, C8.2, C9.2, C10.1, D2.A, D5.A, D6.4 (BLU-C), D6.5 (RED-C), D6.6 (GRN-C), J4.2, J5.1, J8.1 (GND), J9.1 (GND), Q1.2 (E), Q2.2 (S), R9.2, R12.1, R13.2, RPI1.6 (GND), RPI1.9 (GND), RPI1.14 (GND), RPI1.20 (GND), RPI1.25 (GND), RPI1.30 (GND), RPI1.34 (GND), RPI1.39 (GND), U1.4 (AGND), U1.5 (BGND), U2.2 (GND), U3.2 (GND), U4.1 (GNDT), U4.7 (+/-)
GPIO4: RPI1.7 (GPIO4)
GPIO5: J7.1, RPI1.29 (GPIO5)
GPIO6: J6.2, RPI1.31 (GPIO6)
GPIO12: D9.A, R10.2, RPI1.32 (GPIO12)
GPIO13: J6.1, RPI1.33 (GPIO13)
GPIO16: R4.2, RPI1.36 (GPIO16)
GPIO18: R11.1, RPI1.12 (GPIO18)
GPIO22: J7.2, RPI1.15 (GPIO22)
GPIO23: RPI1.16 (GPIO23)
GPIO24: RPI1.18 (GPIO24)
GPIO25: RPI1.22 (GPIO25)
GPIO26: J4.1, RPI1.37 (GPIO26)
LED_BLUE: R5.1, RPI1.38 (GPIO20)
LED_GREEN: R6.1, RPI1.35 (GPIO19)
LED_RED: R7.1, RPI1.40 (GPIO21)
LED_RFID: R14.1, U4.10 (LED)
LOGOUT: J3.1, R4.1, S1.3
unnamed: Q1.1 (B), R14.2
unnamed: JP1.1, LS1.+ (1)
unnamed: LS1.- (2), Q1.3 (C), R8.1
unnamed: D1.C, R8.2
unnamed: D8.A, K1.9, Q2.3 (D)
unnamed: J2.1, K1.6
unnamed: J2.2, K1.10
unnamed: D6.2 (RED-A), R7.2
unnamed: D6.1 (GRN-A), R6.2
unnamed: D6.3 (BLU-A), R5.2
RECT+: D3.C, D4.C, R12.2, U3.1 (IN+)
RELAY: Q2.1 (G), R13.1, RPI1.11 (GPIO17)
RXD: RPI1.10 (RXD), U4.9 (D0)
SCL: J8.4 (SCL), RPI1.5 (SCL), U1.3 (ASCL)
SDA: J8.3 (SDA), RPI1.3 (SDA), U1.2 (ASDA)
SPI_CE0: RPI1.24 (#SPI_CE0)
SPI_CE1: RPI1.26 (#SPI_CE1)
SPI_MISO: RPI1.21 (SPI_MISO)
SPI_MOSI: RPI1.19 (SPI_MOSI)
SPI_SCLK: RPI1.23 (SPI_SCLK)
TXD: RPI1.8 (TXD)
VREF: C8.1, R11.2, U3.3 (IN-)

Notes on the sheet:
GPIO 18 is used by the CURRENT SENSE PWM GPIO 17 is used by the RELAY. GPIO 20, 19, 21 are for the RGB LED.
TinkerMill Longmont, CO
1.4

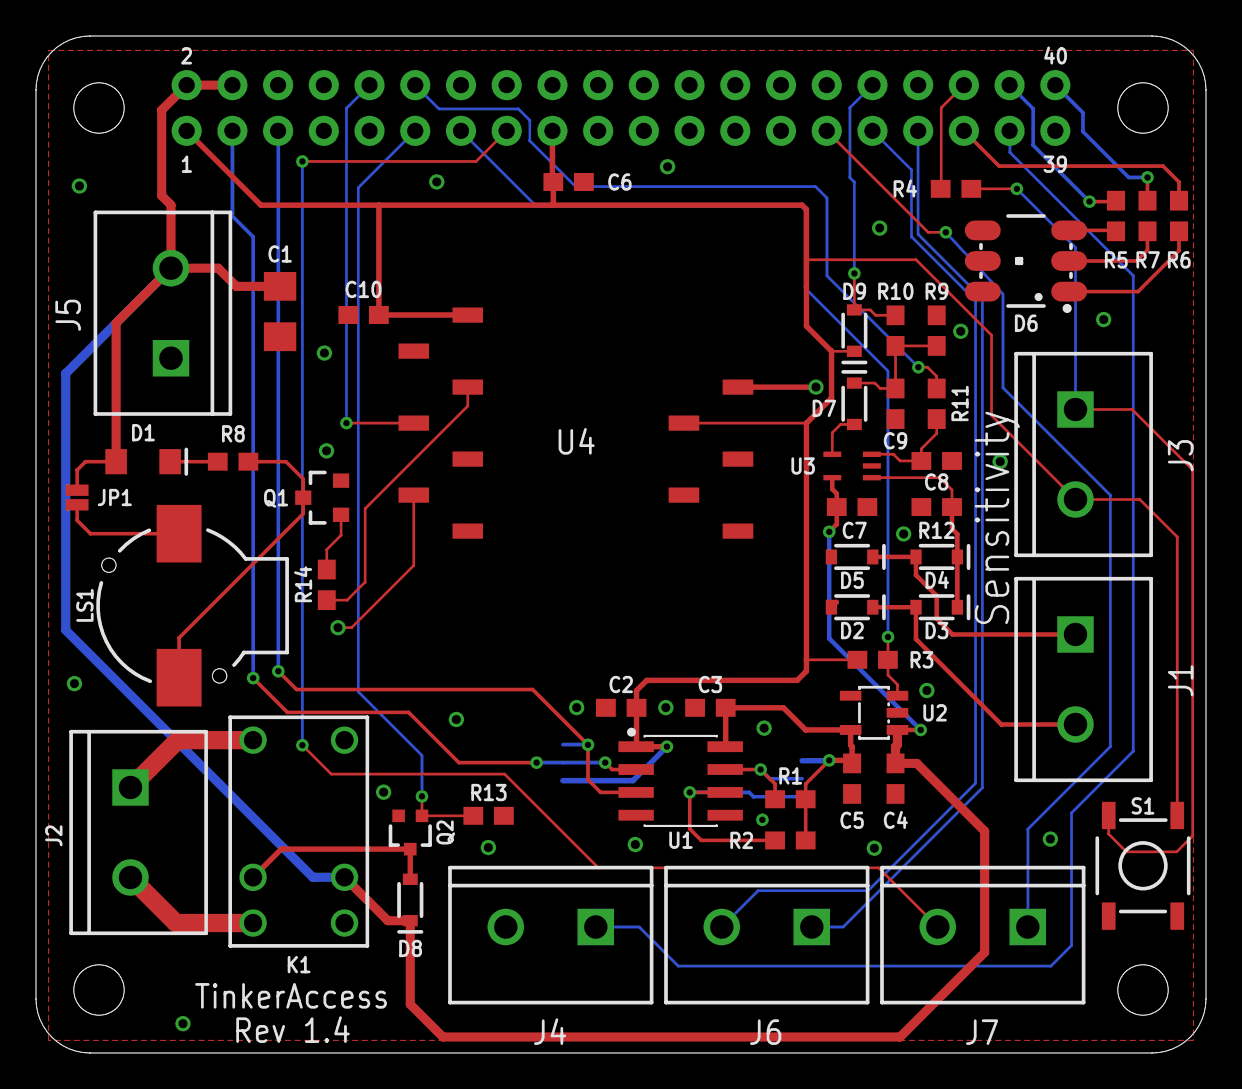
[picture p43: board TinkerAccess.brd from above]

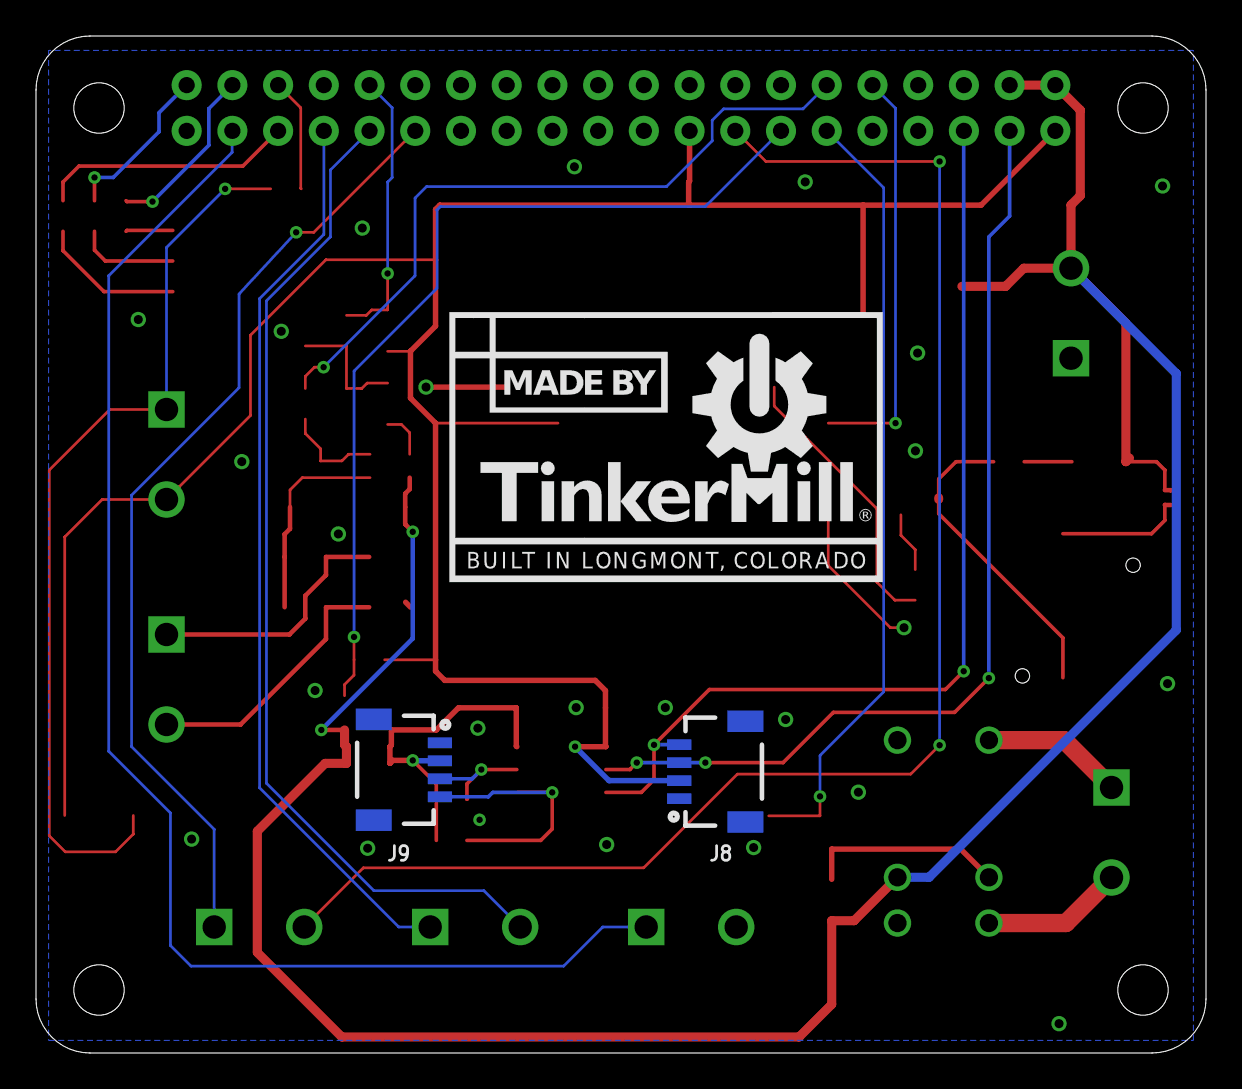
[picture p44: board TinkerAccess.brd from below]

Board: 2 copper layers, 65.0 x 56.5 mm, 54 parts (3 on the bottom side), 40 nets.

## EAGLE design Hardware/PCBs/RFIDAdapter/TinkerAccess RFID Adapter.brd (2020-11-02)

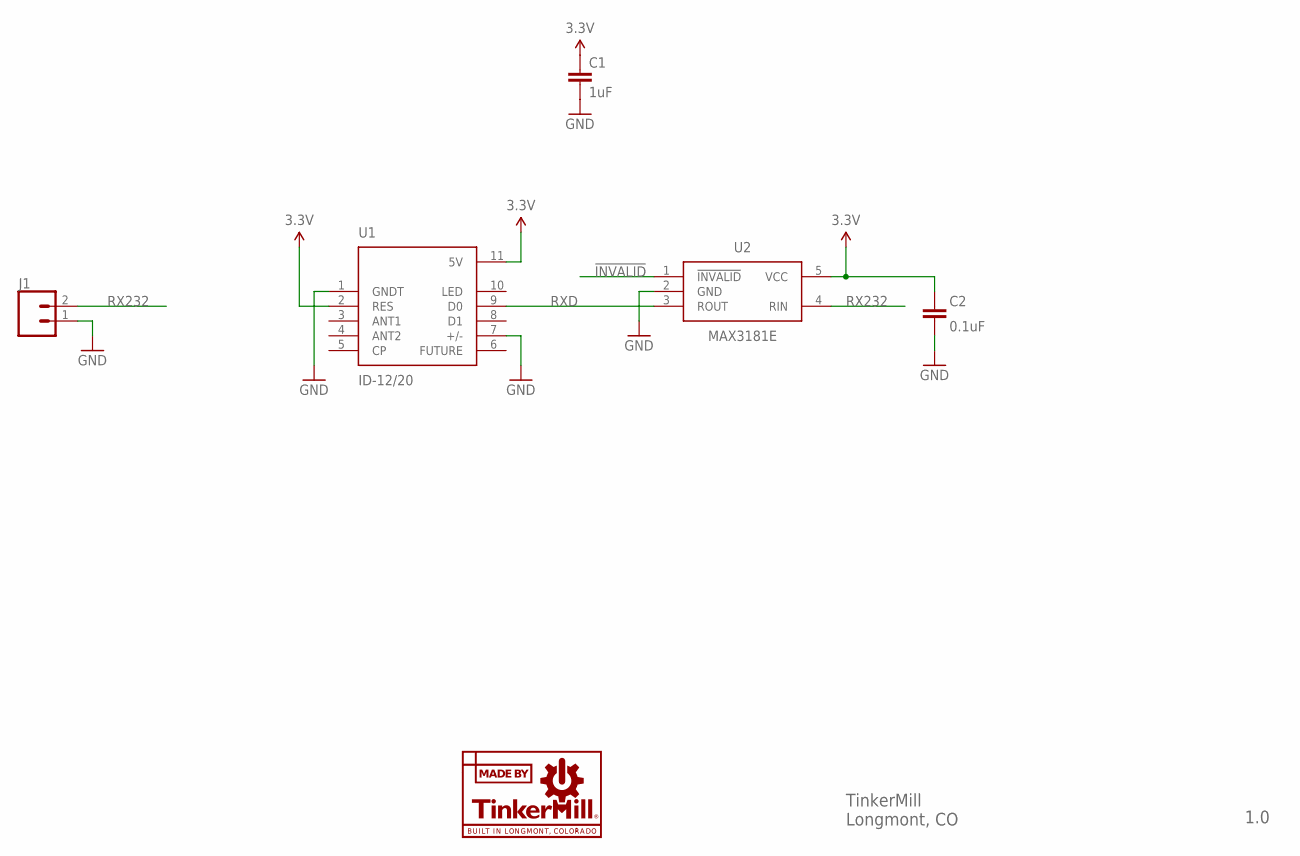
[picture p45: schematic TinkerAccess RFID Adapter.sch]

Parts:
C1: 1uF; 0603
C2: 0.1uF; 0603
J1: CONN_025MM; SCREWTERMINAL-5MM-2
LOGO1: MADE_BY_TINKERMILL
U1: ID-12/20; ID-12
U2: MAX3181E; SOT23-5

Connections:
3.3V: C1.1, C2.2, U1.2 (RES), U1.11 (5V), U2.5 (VCC)
!INVALID: U2.1 (!INVALID)
GND: C1.2, C2.1, J1.1, U1.1 (GNDT), U1.7 (+/-), U2.2 (GND)
RX232: J1.2, U2.4 (RIN)
RXD: U1.9 (D0), U2.3 (ROUT)

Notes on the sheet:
TinkerMill Longmont, CO
1.0

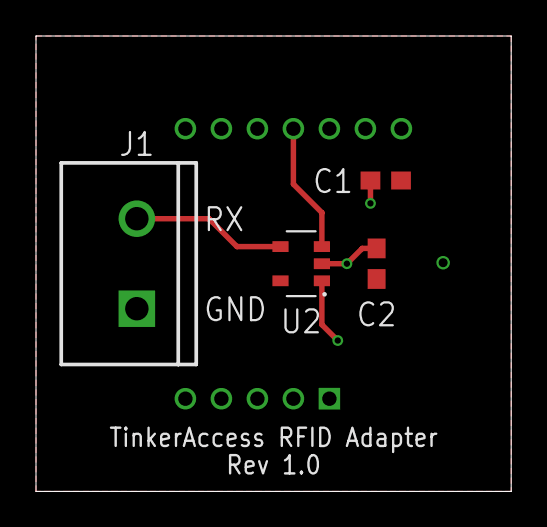
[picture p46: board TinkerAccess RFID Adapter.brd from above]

Board: 2 copper layers, 26.4 x 25.3 mm, 6 parts (1 on the bottom side), 4 nets.

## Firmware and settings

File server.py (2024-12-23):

#!/usr/bin/python

# http://flask.pocoo.org/docs/0.10/patterns/sqlite3/
# http://ryrobes.com/python/running-python-scripts-as-a-windows-service/
# http://stackoverflow.com/questions/23550067/deploy-flask-app-as-windows-service
# http://gouthamanbalaraman.com/blog/minimal-flask-login-example.html

from flask import Flask,g,request,render_template,redirect
import sqlite3
import ConfigParser
import sys
import os
import os.path
import json
import requests
import base64
import csv
import re
from collections import defaultdict, namedtuple
import datetime
from calendar import monthrange
import logging
from threading import Thread

app = Flask("simpleServer")


c = ConfigParser.ConfigParser()
configPath=None

for p in ["/opt/tinkeraccess/server.cfg", "server.cfg"]:
  if os.path.isfile(p):
    configPath=p
    break

if configPath:
  c.read(configPath)
  C_password = c.get('config', 'password')
  C_database = c.get('config', 'db') 
  C_slackPostUrl = c.get('config', 'slackurl')
  c_webcam_username = None
  c_webcam_password = None
  c_imgur_client_id = None
  if c.has_option('config', 'webcam_username'): c_webcam_username = c.get('config', 'webcam_username')
  if c.has_option('config', 'webcam_password'): c_webcam_password = c.get('config', 'webcam_password')
  if c.has_option('config', 'imgur_client_id'): c_imgur_client_id = c.get('config', 'imgur_client_id')

  c_webcam_urls = dict()
  if c.has_section('webcam_urls'):
    if c_webcam_username is None or c_webcam_password is None or c_imgur_client_id is None:
        print("To post webcam images, `webcam_username`, `webcam_password`,\n" +
              "and `imgur_client_id` must all be specified in the `config`\n" +
              "section")
    else: c_webcam_urls = dict(c.items(section='webcam_urls'))

else:
  print("config server.cfg not found")
  sys.exit(1)


######### Slack function #############

def post_to_slack(message):
  try:
    requests.post(C_slackPostUrl, data=json.dumps(message))
  except Exception as e:
    logging.exception(e)

######### Database functions #########

def init_db():
  with app.app_context():
    if os.path.isfile("/opt/tinkeraccess/db.db"):
      os.remove("/opt/tinkeraccess/db.db")

    db = get_db()
    with app.open_resource('schema.sql', mode='r') as f:
      db.cursor().executescript(f.read())
    db.commit()

def exec_db(query):
  db = get_db()
  db.cursor().execute(query)
  db.commit()

def query_db(query, args=(), one=False):
    cur = get_db().execute(query, args)
    rv = cur.fetchall()
    cur.close()
    return (rv[0] if rv else None) if one else rv

def get_db():
    db = getattr(g, '_database', None)
    if db is None:
        db = g._database = sqlite3.connect(C_database)
    return db

def insert(table, fields=(), values=()):
  # g.db is the database connection
  cur = get_db().cursor()
  query = 'INSERT INTO %s (%s) VALUES (%s)' % (
  table,
    ', '.join(fields),
    ', '.join(['?'] * len(values))
  )
  cur.execute(query, values)
  get_db().commit()
  id = cur.lastrowid
  cur.close()
  return id

def addNewUser(code, deviceid):
  o = query_db("select code from newuser where code='%s'" % code)
  if len(o) == 0:
    o = query_db("select code from user where code='%s'" % code)
    if len(o) == 0:
      exec_db("insert into newuser (code,deviceID) values ('%s', %s)" % (code, deviceid) )


######### Webserver functions #########

@app.teardown_appcontext
def close_connection(exception):
    db = getattr(g, '_database', None)
    if db is not None:
        db.close()

# logout
@app.route("/device/<deviceid>/logout/<uid>")
def deviceLogout(deviceid, uid):
  output = query_db("select device.name from device where id=%s" % deviceid)
  exec_db("insert into log (message) values ('logout:%s:%s')" % (deviceid,uid) )

  message_content = {'text': '{} is now available'.format(output[0][0])}
  if output[0][0] in c_webcam_urls:
      image_url = captureImage(c_webcam_urls[output[0][0]])
      if len(image_url) > 0:
          message_content['attachments'] = [{
              'fallback': 'Webcam image of {}'.format(output[0][0]),
              'image_url': image_url
              }]

  t = Thread(target=post_to_slack, args=(message_content,))
  t.start()

  return ""

# given a device and a rfid code return if there is access to that device
# this is the login
@app.route("/device/<deviceid>/code/<code>")
def deviceCode(deviceid,code):

  deviceinfo = query_db("select name,allUsers,lockout,lockout_start,lockout_end from device where id=%s" % deviceid)
  
  if len(deviceinfo) == 0:
    # Device ID not found, so deny access
    return json.dumps( {'devicename': 'none', 'username': 'none', 'userid': -1, 'time': 0 } )

  devicename    = deviceinfo[0][0]
  allusers      = deviceinfo[0][1]
  lockout       = deviceinfo[0][2]
  lockout_start = deviceinfo[0][3]
  lockout_end   = deviceinfo[0][4]

  if lockout == 2:
    # Device is locked out, so deny access
    return json.dumps( {'devicename': 'none', 'username': 'none', 'userid': -1, 'time': 0 } )

  # Customize the query based upon the device settings
  if lockout == 0:
    # Device access is not time limited

    if allusers:
      # Device access is granted to all users and is not time limited
      output = query_db("select user.name, user.id from user where user.code='%s' and user.status IN ('A','S')" % (code))
      
    else:
      # Device access is granted at an individual user level and is not time limited
      output = query_db("select user.name, user.id, deviceAccess.time from deviceAccess join device on device.id=deviceAccess.device join user on user.id = deviceAccess.user \
                         where user.code='%s' and user.status IN ('A','S') and device.id=%s" % (code,deviceid))

  elif lockout == 1:
    # Device access is time limited

    now = datetime.datetime.now()
    now = 100 * now.hour + now.minute

    x = re.split(':| ',lockout_start)
    start_time = 100*((int(x[0]) % 12) + (12 if x[2]=="PM" else 0)) + int(x[1])

    x = re.split(':| ',lockout_end)
    end_time = 100*((int(x[0]) % 12) + (12 if x[2]=="PM" else 0)) + int(x[1])
    
    if start_time <= end_time:
      during_time_limit = start_time <= now < end_time
    else:
      during_time_limit = now >= start_time or now < end_time

    if during_time_limit:
      # Current time is during the time limited range, only select those with 24hr access

      if allusers:
        # Device access is granted to all users only with 24 hr access during time limited range
        output = query_db("select user.name, user.id from user where user.code='%s' and user.status='S'" % (code))

      else:
        # Device access is granted at an individual user level only with 24 hr access during time limited range
        output = query_db("select user.name, user.id, deviceAccess.time from deviceAccess join device on device.id=deviceAccess.device join user on user.id = deviceAccess.user \
                          where user.code='%s' and user.status='S' and device.id=%s" % (code,deviceid))

    else:
      # Device access is time limited but current time is not within the range

      if allusers:
        # Device access is granted to all users, outside the time limited range
        output = query_db("select user.name, user.id from user where user.code='%s' and user.status IN ('A','S')" % (code))

      else:
        #  Device access is granted at an individual user level, outside the time limited range
        output = query_db("select user.name, user.id, deviceAccess.time from deviceAccess join device on device.id=deviceAccess.device join user on user.id = deviceAccess.user \
                          where user.code='%s' and user.status IN ('A','S') and device.id=%s" % (code,deviceid))

  else:
    # Unknown lockout status, deny access
    return json.dumps( {'devicename': 'none', 'username': 'none', 'userid': -1, 'time': 0 } )
    
  if len(output) == 0:
    # User badge code not found, or is inactive, or does not have 24hr access, so deny access
    addNewUser(code, deviceid)
    return json.dumps( {'devicename': 'none', 'username': 'none', 'userid': -1, 'time': 0 } )
      
  # User badge code found, so grant access

  username = output[0][0]
  userid   = output[0][1]
  accesstime = 100 if allusers else output[0][2]
  
  # Send the data to slack
  message_content = {'text': '{} is now in use by {}'.format(devicename, username)}
  if devicename in c_webcam_urls:
    image_url = captureImage(c_webcam_urls[devicename])
    if len(image_url) > 0:
      message_content['attachments'] = [{
        'fallback': 'Webcam image of {}'.format(devicename),
        'image_url': image_url
      }]

  t = Thread(target=post_to_slack, args=(message_content,))
  t.start()

  # log it to the database
  exec_db("insert into log (message) values ('login:%s:%s')" % (deviceid, userid) )

  return json.dumps(
    {
      'devicename': devicename,
      'username': username,
      'userid': userid,
      'time': accesstime
    }
  )

@app.route("/")
def defaultRoute():
  return render_template('admin_login.html')

@app.route("/checkLogin/<user>/<password>" )
def checkLogin(user,password):
  if password == C_password:
    return "true"
  else:
    return "false"

# given a name and badge code, add the user to the database
# and clear out any perms that id might have had in the past
def userAdd(name, badgeCode):
  exec_db("insert into user (name,code) values ('%s','%s')" % (name, badgeCode))

  # if the database is dirty, make sure that any existing records are cleared out
  userAccess = query_db("select id from user where code='%s'" % badgeCode)
  if len(userAccess) > 0:
    exec_db("delete from deviceAccess where user=%s" % userAccess[0][0] )

@app.route("/admin/addUser/<userid>/name/<name>")
def addUser(userid, name):
  if request.cookies.get('password') != C_password:
    return False

  name = name.strip()
  output = query_db("select code from newuser where id=%s" % userid)
  badgeCode = output[0][0]

  output = query_db("select code from user where name='%s' and status IN ('A','S')" % name)
  
  if len(output) == 0:
    # No active user with same name, go ahead and add this user id
    userAdd(name,badgeCode)
    exec_db("delete from newuser where id=%s" % userid)
    return redirect("/admin/interface/user")
  else:
    # User with same name already active, popup error window
    existingBadge = output[0][0]
    return redirect("/admin/interface/newuser/modal/useractive/%s/%s/%s" % (name, existingBadge, badgeCode))
  
@app.route("/admin/loadcsv", methods=['POST'])
def loadCSV():
  if request.cookies.get('password') != C_password:
    return False

  data = request.form['csv']

  # stip leading , if it is there
  data = map(lambda x: re.sub('^,', '', x), data.split("\n"))
  reader = csv.reader(data, delimiter=',')
  for row in reader:
    if len(row) == 0:
      continue

    name = row[0].strip()
    code = row[1].strip()

    output = query_db("select code from user where code='%s'" % code)
    if len(output) == 0:
      # Badge does not already exist in database
      output = query_db("select name from user where name='%s' and status IN ('A','S')" % name)
      if len(output) == 0:
        # Name does not exist in database of an active user
        userAdd(name, code)
        
  return redirect("/admin/interface/user")


"""
when a trainer logs in, he can register anyone on this device as a user
http://localhost:5000/admin/marioStar/1/150060E726B4/0/2
"""
@app.route("/admin/marioStar/<trainerid>/<trainerBadge>/<deviceid>/<userBadge>")
def marioStarMode(trainerid,trainerBadge, deviceid, userBadge):
  trainer = query_db("select user.id from user join deviceAccess on deviceAccess.user=user.id where user.id=%s and user.code='%s' and user.status IN ('A','S') and deviceAccess.trainer=1 and deviceAccess.device=%s" % (trainerid, trainerBadge, deviceid))
  
  # the user must already exist in the system
  userid = query_db("select id from user where code='%s' and status IN ('A','S')" % (userBadge) )

  #print("userId", userid)
  #print("lenUserId=1", len(userid))
  #print("trainer", trainer)
  #print("lentrainer=1", len(trainer))

  if len(userid) == 1 and len(trainer) == 1:
    userid = userid[0][0]
    exec_db("delete from deviceAccess where user=%s and device=%s" % (userid, deviceid))
    exec_db("insert into deviceAccess (user,device,time) values (%s, %s, 100)" % (userid, deviceid))
    return "true"
  else:
    return "false"

@app.route("/admin/addUserAccess/<userid>/<deviceid>")
def addUserAccess(userid, deviceid):
  if request.cookies.get('password') != C_password:
    return False

  exec_db("delete from deviceAccess where user=%s and device=%s" % (userid, deviceid))
  exec_db("insert into deviceAccess (user,device,time) values (%s, %s, 100)" % (userid, deviceid))
  return redirect("/admin/interface/userAccess/%s" % userid)

@app.route("/admin/toggle24Hr/user/<userid>")
def toggle24HrAccess(userid):
  if request.cookies.get('password') != C_password:
    return False

  output = query_db("select status from user where id=%s" % userid)

  if output[0][0] == 'A':
    exec_db("update user set status='S' where id=%s" % userid)
  elif output[0][0] == 'S':
    exec_db("update user set status='A' where id=%s" % userid)
  
  return redirect("/admin/interface/userAccess/%s" % userid)

@app.route("/admin/removeTrainer/<userid>/<deviceid>")
def delUserTrainerAccess(userid, deviceid):
  if request.cookies.get('password') != C_password:
    return False

  exec_db("update deviceAccess set trainer=0 where user=%s and device=%s" % (userid, deviceid))
  return redirect("/admin/interface/userAccess/%s" % userid)

@app.route("/admin/addTrainer/<userid>/<deviceid>")
def addUserTrainerAccess(userid, deviceid):
  if request.cookies.get('password') != C_password:
    return False

  exec_db("update deviceAccess set trainer=1 where user=%s and device=%s" % (userid, deviceid))
  return redirect("/admin/interface/userAccess/%s" % userid)

@app.route("/admin/delUserAccess/<userid>/<deviceid>")
def delUserAccess(userid, deviceid):
  if request.cookies.get('password') != C_password:
    return False

  exec_db("delete from deviceAccess where user=%s and device=%s" % (userid, deviceid))
  return redirect("/admin/interface/userAccess/%s" % userid)

@app.route("/admin/delNewUser/<userid>")
def delNewUser(userid):
  if request.cookies.get('password') != C_password:
    return False

  exec_db("delete from newuser where id=%s" % userid)
  return redirect("/admin/interface/newuser")

@app.route("/admin/delUser/<userid>")
def delUser(userid):
  if request.cookies.get('password') != C_password:
    return False

  exec_db("delete from user where id=%s" % userid)
  return redirect("/admin/interface/inactiveuser")

@app.route("/admin/activateUser/<userid>")
def activateUser(userid):
  if request.cookies.get('password') != C_password:
    return False

  # Get the name and badge code to be activated
  output = query_db("select name,code from user where id=%s" % userid)

  name = output[0][0]
  newbadge = output[0][1]

  output = query_db("select code from user where name='%s' and status IN ('A','S')" % name)
  
  if len(output) == 0:
    # No active user with same name, make this user id active
    exec_db("update user set status='A' where id=%s" % userid)
    return redirect("/admin/interface/inactiveuser")
  else:
    # User with same name already active, popup error window
    badge = output[0][0]
    return redirect("/admin/interface/inactiveuser/modal/useractive/%s/%s/%s" % (name, badge, newbadge))

@app.route("/admin/deactivateUser/<userid>")
def deactivateUser(userid):
  if request.cookies.get('password') != C_password:
    return False

  exec_db("update user set status='I' where id=%s" % userid)
  return redirect("/admin/interface/user")

@app.route("/admin/deviceUnlimitedHr/<deviceid>")
def deviceUnlimitedHr(deviceid):
  if request.cookies.get('password') != C_password:
    return False

  exec_db("update device set lockout=0 where id=%s" % deviceid)
  return redirect("/admin/interface/devices")

@app.route("/admin/deviceLimitedHr/<deviceid>")
def deviceLimitedHr(deviceid):
  if request.cookies.get('password') != C_password:
    return False

  exec_db("update device set lockout=1 where id=%s" % deviceid)
  return redirect("/admin/interface/devices")

@app.route("/admin/deviceLockout/<deviceid>")
def deviceLockout(deviceid):
  if request.cookies.get('password') != C_password:
    return False

  exec_db("update device set lockout=2 where id=%s" % deviceid)
  return redirect("/admin/interface/devices")

@app.route("/admin/deviceLockoutTimes/<deviceid>/time/<start>/<end>")
def deviceLockoutTimes(deviceid, start, end):
  if request.cookies.get('password') != C_password:
    return False

  exec_db("update device set lockout_start='%s', lockout_end='%s' where id=%s" % (start, end, deviceid))
  return redirect("/admin/interface/devices")

@app.route("/admin/interface/newuser")
def newUserInterface():
  if request.cookies.get('password') != C_password:
    return redirect("/")

  users = query_db("select newuser.id,newuser.code,device.name from newuser left join device on newuser.deviceID = device.id")
  #users = query_db("select id,code,deviceID from newuser")
  return render_template('admin_newuser.html', users=users)

@app.route("/admin/interface/inactiveuser")
def inactiveUserInterface():
  if request.cookies.get('password') != C_password:
    return redirect("/")

  users = query_db("select name,code,id from user where status='I' order by name")
  return render_template('admin_inactiveuser.html', users=users)

@app.route("/admin/interface/inactiveuser/modal/deluser/<userid>/<name>/<badge>")
def delUserModal(userid, name, badge):
  if request.cookies.get('password') != C_password:
    return redirect("/")

  users = query_db("select name,code,id from user where status='I' order by name")
  return render_template('modal_deluser.html', users=users, userid=userid, name=name, badge=badge)

@app.route("/admin/interface/inactiveuser/modal/useractive/<name>/<badge>/<newbadge>")
def userActiveModal(name, badge, newbadge):
  if request.cookies.get('password') != C_password:
    return redirect("/")

  users = query_db("select name,code,id from user where status='I' order by name")
  return render_template('modal_useractive.html', users=users, name=name, badge=badge, newbadge=newbadge)

@app.route("/admin/interface/newuser/modal/useractive/<name>/<badge>/<newbadge>")
def newuserActiveModal(name, badge, newbadge):
  if request.cookies.get('password') != C_password:
    return redirect("/")

  users = query_db("select id,code,deviceID from newuser")
  return render_template('modal_newuseractive.html', users=users, name=name, badge=badge, newbadge=newbadge)

@app.route("/admin/interface/user")
def adminInterface():
  if request.cookies.get('password') != C_password:
    return redirect("/")

  users = query_db("select name,code,id,status from user where status IN ('A','S') order by status desc")
  return render_template('admin_user.html', users=users)

@app.route("/admin/interface/userAccess/<userid>")
def userAccessInterface(userid):
  if request.cookies.get('password') != C_password:
    return redirect("/")

  # list of all the devices the user could have access to
  allDevices = query_db("select id, name from device where allUsers=0 except select device.id, device.name from deviceAccess join device on device.id=deviceAccess.device join user on user.id = deviceAccess.user where deviceAccess.user=%s and device.allUsers=0" % userid)

  # list of devices with all user access
  allUserDevices = query_db("select name from device where allUsers=1")
  
  # list of devices the user currently has access to
  userAccess = query_db("select user.name, user.id, device.id, device.name, deviceAccess.time, deviceAccess.trainer from deviceAccess join device on device.id=deviceAccess.device join user on user.id = deviceAccess.user where deviceAccess.user=%s and device.allUsers=0" % userid)
  
  username   = query_db("select user.name from user where id=%s" % userid)[0][0]

  s = query_db("select user.status from user where id=%s" % userid)[0][0]
  if s=='A':
    userstatus = "Active"
  elif s=='S':
    userstatus = "Active - 24 Hr"
  elif s=='I':
    userstatus = "Inactive"
  else:
    userstatus = "Unknown"
    
  return render_template('admin_userAccess.html', devices=allDevices, access=userAccess, alluserdevices=allUserDevices, userid=userid, username=username, userstatus=userstatus, ustatus=s)

@app.route("/admin/interface/devices")
def deviceInterface():
  if request.cookies.get('password') != C_password:
    return redirect("/")

  devices = query_db("select id,name,allUsers,lockout,lockout_start,lockout_end from device")
  return render_template('admin_devices.html', devices=devices)

@app.route("/admin/interface/deviceAccess/<deviceid>")
def deviceAccessInterface(deviceid):
  if request.cookies.get('password') != C_password:
    return redirect("/")

  devicename = query_db("select device.name from device where id=%s" % deviceid)[0][0]
  userAccess = query_db("select user.id, user.name, user.code, deviceAccess.trainer from deviceAccess join device on device.id=deviceAccess.device join user on user.id = deviceAccess.user where deviceAccess.device=%s and device.allUsers=0 and user.status IN ('A','S') order by deviceAccess.trainer desc" % deviceid)
  
  return render_template('admin_deviceAccess.html', access=userAccess, deviceid=deviceid, devicename=devicename)
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

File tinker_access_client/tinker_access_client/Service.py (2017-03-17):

#!/usr/bin/env python

# Reference: https://wiki.debian.org/LSBInitScripts

### BEGIN INIT INFO
# Provides:          tinker-access-client
# Required-Start:    $all
# Required-Stop:     $remote_fs $syslog
# Default-Start:     2 3 4 5
# Default-Stop:      0 1 6
# Short-Description: tinker-access-client
# Description:       The tinker-access-client service is responsible for coordinating communication
# between RPi's modules (i.e. RFID reader, LCD, power relays etc..) and the remote tinker_access_server.
### END INIT INFO

import os
import sys
from State import State
from PackageInfo import PackageInfo
from ClientLogger import ClientLogger
from ClientDaemon import ClientDaemon
from CommandHandler import CommandHandler
from ClientOptionParser import ClientOptionParser, Command


def __handle_status_command(opts, args):
    status = ClientDaemon.status(opts, args)
    if status:
        __handle_command_response(['{0}\n'.format(status)], 0)
    else:
        __handle_command_response(['{0}\n'.format(State.TERMINATED)], 1)


def __handle_update_command(opts, args):
    (messages, exit_code) = ClientDaemon.update(opts, args)
    __handle_command_response(messages, exit_code)


def __handle_start_command(opts, args):
    (messages, exit_code) = ClientDaemon.start(opts, args)
    __handle_command_response(messages, exit_code)


def __handle_command_response(messages, exit_code=0):
    if messages:
        for msg in messages:
            sys.stdout.write(msg)
            sys.stdout.flush()
    sys.exit(exit_code)


def run():
    if os.geteuid() != 0:
        sys.stdout.write(
            'You need to have root privileges to run {0} commands.\n'
            'Please try again, this time using \'sudo\'.\n'.format(PackageInfo.pip_package_name))
        sys.stdout.flush()
        sys.exit(1)

    (opts, args) = ClientOptionParser().parse_args()
    logger = ClientLogger.setup(opts)

    try:
        with CommandHandler(opts, args) as handler:
            handler.on(Command.STOP, ClientDaemon.stop)
            handler.on(Command.START, __handle_start_command)
            handler.on(Command.STATUS, __handle_status_command)
            handler.on(Command.UPDATE, __handle_update_command)
            handler.on(Command.REMOVE, ClientDaemon.remove)
            handler.on(Command.RESTART, ClientDaemon.restart)
            return handler.handle_command()

    except Exception as e:
        logger.exception(e)
        sys.stdout.write(str(e))
        sys.stdout.flush()
        sys.exit(1)

if __name__ == '__main__':
    run()

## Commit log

2015-07-12 initial scanner
    [scan.cfg]
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2015-11-04 changes for IP address
    [scan.cfg]
2015-11-18 removing testing parts
    [run.cfg]
2015-11-19 bug deleting wrong user
    [serv.py]
2016-01-23 push to slack
    [run.cfg]
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2016-01-23 fixing template for log
    [serv.py]
2016-01-30 mostly working
    [client.cfg]
2016-01-31 cleanup file names
    [server.cfg]
2016-01-31 device manager added back
2016-02-12 gave server static ip
    [client.cfg]
2016-02-28 Update client.py
    Adding Current Sense Technology™ and LED fix
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2016-03-04 Added coast-down delay functionality
    If a logout request happens while the machine is running, this added
    functionality ensures that the logout event doesn't execute until a
    coast-down period elapses.
    [client.cfg]
2016-03-06 Updated RFID Wiring Diagram - resistor on coil
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2016-03-13 Verbose output on machine down, and global for currentBadge
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2016-05-11 adding run.cfg back
    [run.cfg]
2016-05-11 Add trainer status from website, api point to have trainer add people
    [server.cfg]
2016-05-15 lowered count cycle on reset button hold down
    went from 2000 to 20 since there is a .1 sleep cycle each time it loops... so I only have to hold down for 2 second instead of 200 :)
2016-05-16 place abs path back into server config for db
    [server.cfg]
2016-11-02 Updated circuit schematics
    Improved current sense circuit and corrected LED resistor values.
2017-03-16 refactor: refactoring tinker_access_client...
    [client.cfg]
2017-04-02 (issue): #11 - Current Sense/Coastdown Time not implemented correctly
    [Client.py, ClientDaemon.py, ClientOptionParser.py]
2017-04-05 Fix reboot delay to 5 minutes instead of 5 seconds
    [ClientOptionParser.py]
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2017-05-11 Update VirtualDevice in integration test utils to match DeviceApi
2017-05-11 Fix typo in LcdApi.py
    [LcdApi.py]
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2017-05-18 Add fritzing file and exported images
    [tinkerAccess.fzz]
2017-07-12 Add new Fritzing file for Raspberry Pi Hat design
    [tinkerAccess-Hat.fzz]
2017-07-12 Add Hat board exports
    [tinkerAccess-Hat_contour.gm1, tinkerAccess-Hat_copperBottom.gbl, tinkerAccess-Hat_copperTop.gtl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]
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2017-07-18 Add power to U2 LM393 thanks to Tyler
    [tinkerAccess-Hat.fzz]
2017-07-19 Fix issues found by Tyler Dow and Don Vukovic
    [tinkerAccess-Hat.fzz]
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2017-07-19 Update exported PCB files
    [tinkerAccess-Hat_copperBottom.gbl, tinkerAccess-Hat_copperTop.gtl, tinkerAccess-Hat_maskBottom.gbs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]
2019-12-19 Create TinkerAccess.brd
    Version V1_2 from Don Vukovic
    [TinkerAccess.brd]
2019-12-19 Create TinkerAccess.sch
    Version V1.2b from Don Vukovic
    [TinkerAccess.sch]
2020-02-11 Added Machine Shop TinkerAccess documentation
    [Machine Shop TinkerAccess.sch]
2020-02-20 Finshied Removing HW bugs
    Fixed missing trace, Pad sizes for ADCMP371 and SI8600. Also added a trace for the 3.3V en to a GPIO for restarting the
    [TinkerAccess.sch]
2020-02-23 bugfix to get correct PID to kill on shutdown
    Running `/opt/tinkeraccess/server.py` directly saves the wrong PID in
    `/var/run/tinkerAccessServer.pid`, which is later used to kill the
    server when the service is stopped. Instead, running the server via
    `python /opt/tinkeraccess/server.py` reports the correct PID.
2020-02-26 Added --noreload option to server
    Prevents zombie server when run from /etc/init.d/tinkerserver. The Flask
    server by default runs a child process, which is the actual webserver,
    so that the parent can monitor the server files and restart the child
    when they change. This, however, interferes with start-stop-daemon's
    ability to stop the server. This change fixes that behavior.
    [server.py]
2020-05-23 TinkerBoard Update
    Fixed Drill Hole size to match Design rules.
    Fixed Pad sizes.
    Fixed AirWires.
    [TinkerAccess.brd]
2020-05-24 added pulldown
    Added pulldown resistor to 3v3 Enable line
    [TinkerAccess.brd, TinkerAccess.sch]
2020-05-28 Modified schematic to connect RPi power supply to load side of disconnect.
    [Machine Shop TinkerAccess.sch]
2020-05-29 Cleaned up schematic notes
    [Machine Shop TinkerAccess.sch]
2020-06-18 Merged in local changes found on laser cutter, lathe, shopbot, and sla door nodes.
2020-06-19 Updates to machine shop TA schematic.
    [Machine Shop TinkerAccess.sch]
2020-06-21 Uploaded standard enclosure datasheet and portrait face plate
    [TinkerAccess Face Plate - Portrait.dxf]
2020-06-27 Added support for new SparkFun LCD-14072 SerLCD display Added support for an E-STOP input pin to detect an event and automatically logout the current user Added support for the 3.3V enable pin added 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
    [Client.py, ClientOption.py, ClientOptionParser.py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]
2020-06-27 Moved E-Stop input to GPIO6 Added machine shop faceplate DXF file
    [Machine Shop TinkerAccess.sch, TinkerAccess_Faceplate_Vertical.dxf]
2020-06-27 Fixed test assertions for training mode
    [CustomAssertions.py]
2020-07-02 Added a configurable feature where a new user can override and take over the current user session. Added some thread locking semaphores around timers related to the LCD display to prevent race condit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
    [Client.py, ClientOption.py, ClientOptionParser.py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]
2020-07-14 Updated machine shop schematic with bypass detect changes
    [Machine Shop TinkerAccess.sch]
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2020-08-05 prototype of image capture/posting
    [server.cfg]
2020-08-06 cleanup to webcam interface
    [server.cfg]
2020-08-06 moved server.cfg to example_server.cfg
    [example_server.cfg]
2020-08-14 Changed Travis CI config file so that a wheel distribution is not attempted to be built for the tinker-access client. Recent pip versions will attempt a wheel build first before defaulting back to th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
2020-08-14 Added alarm beacon wiring to machine shop TinkerAccess schematic
    [Machine Shop TinkerAccess.sch]
2020-08-14 fixes to run without webcam
    [server.py]
2020-08-14 even better config management
    [example_server.cfg]
2020-08-20 Changes for PCB spin with a PWM based current sense detect setting
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2020-09-08 Changes for v1.4 of TinkerAccess PCB
    [TinkerAccess.brd, TinkerAccess.sch]
2020-11-02 Added remote RFID PCBs
    [TinkerAccess RFID Adapter.brd, TinkerAccess RFID Adapter.sch, TinkerAccess Remote RFID.brd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]
2020-12-02 Fixed bug with new 'use_pgm_current_threshold' config option. Added RGB LED Driver PCB.
    [TinkerAccess RGB LED Driver.brd, TinkerAccess RGB LED Driver.sch]
2020-12-06 Changes to server to support device authentication to all users in the database
2020-12-06 Added device user access interface pages to web admin server
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2021-03-04 Updated final front door and machine shop schematics, BOM, and config files
    [Front Door TinkerAccess.sch, Front_Door_TinkerAccess_Backplate.dxf, Front_Door_TinkerAccess_Faceplate.dxf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]
2021-04-21 Added Shopbot schematics, added PCB BOMs, and updated machine shop schematics
    [Machine Shop TinkerAccess.sch, ShopBot TinkerAccess.sch]
2021-05-04 For all updated nodes, updated config files to change reboot on error time from 300 minutes to 5 minutes. Added schematic and BOM for laser cutter implementation.
    [Laser Cutter TinkerAccess.sch]
2021-06-06 Fixed some documentation errors, added faceplate dxf files.
    [Machine Shop TinkerAccess.sch, Remote_RFID_TinkerAccess_Faceplate.dxf, TinkerAccess_Faceplate_Horizontal.dxf]
2021-06-24 Added documentation for table saw implementation
    [Table Saw TinkerAccess.sch]
2021-07-01 Added schematic and documentation for jointer/planer and wood lathe upgrades. Added datasheets for woodshop door parts.
    [Jointer Planer TinkerAccess.sch, Wood Lathe TinkerAccess.sch]
2021-07-30 Added woodshop door schematic, BOM, and config file
    [Woodshop Door TinkerAccess.sch]
2021-09-24 Fix a bug on the server, where the server was not responding to clients when the internet was down because the Slack hook connection failed.
    [server.py]
2021-12-01 Added schematic and documentation for pottery door.
    [Pottery Door TinkerAccess.sch]
2022-06-25 Run the server Slack webhook posts in a thread. This is done so that the response to the client is not held up by Slack being unreachable and the client timing out waiting for a reply. The response t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
    [server.py]
2022-08-02 Added a feature where users can be deactivated instead of deleting. Also added timed access to devices and ability to lockout for maintenance. Also added 24hr access option to users to override devic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
2022-12-15 Captured changes to the door config files. Doors are no longer able to be held unlocked. The exception is the front door which can be held unlocked during tour hours and orientation. A cron job runs 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
2023-01-14 Added W Bay Door documentation
    [W Bay Door TinkerAccess.sch]
2023-03-03 Added Unit C North Door documentation
    [Unit C North Door TinkerAccess.sch]
2023-06-01 Added Powermatic Bandsaw documentation
    [Powermatic Bandsaw TinkerAccess.sch]
2023-06-15 Swapped around monochrome and RGB LCD displays between doors and machines. Updated BOM and config files to reflect these changes.
2023-12-07 Added Welder documentation
    [Welder TinkerAccess.sch]
2024-03-14 Cleaned up PCB BOMs. Added JLCPCB part numbers.
2024-12-23 BUGFIX: deviceUsageSummary will now work in december. TESTING: Added unit tests for ToolSummaryInterface for bugfix TESTING: Added Hurl tests for most (all?) API endpoints, along with test data CLEAN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
    [server.cfg]

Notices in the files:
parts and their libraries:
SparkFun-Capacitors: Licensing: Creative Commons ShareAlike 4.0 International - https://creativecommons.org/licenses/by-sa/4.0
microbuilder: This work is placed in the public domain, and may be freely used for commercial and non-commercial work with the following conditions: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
